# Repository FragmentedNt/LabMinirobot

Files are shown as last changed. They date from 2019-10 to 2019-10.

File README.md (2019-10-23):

# What's this

* sn研でやってる子供向けLEGOロボットのソースとか回路とか機械とか

# 数増やしたいんだけど

1. CircuitCase/Case1_2_9V2.stlおよびCircuitCase/Cover3.ncdを印刷/切削
1. Circuit_v1/ にあるGコードで基板削ってはんだ付け
1. Arduino nanoを用意してminirobo_rmlab/minirobo_rmlab.inoを書き込み
1. SBDBT(3.3V/5V問わず)を用意する
1. MPLAB IPEで sbdbt_ps3_v4/sbxbt_ps3.X/dist/default/production/sbxbt_ps3.X.production.hexを書き込む
1. Done!

# 改善要望

* 回路ケースここまで大きくなくていい
  * LEGOポッチつけたのは大失敗なので消して適当なLEGO板貼り付けるのがベスト
* DCジャック，配線通してはんだ付けするのクソでは？
  * ほんまそれな
* TA8428Kがディスコン
  * 8SOICのイカした後継ICが出てるはず

# 連絡先

* fragmentednt@zoho.com

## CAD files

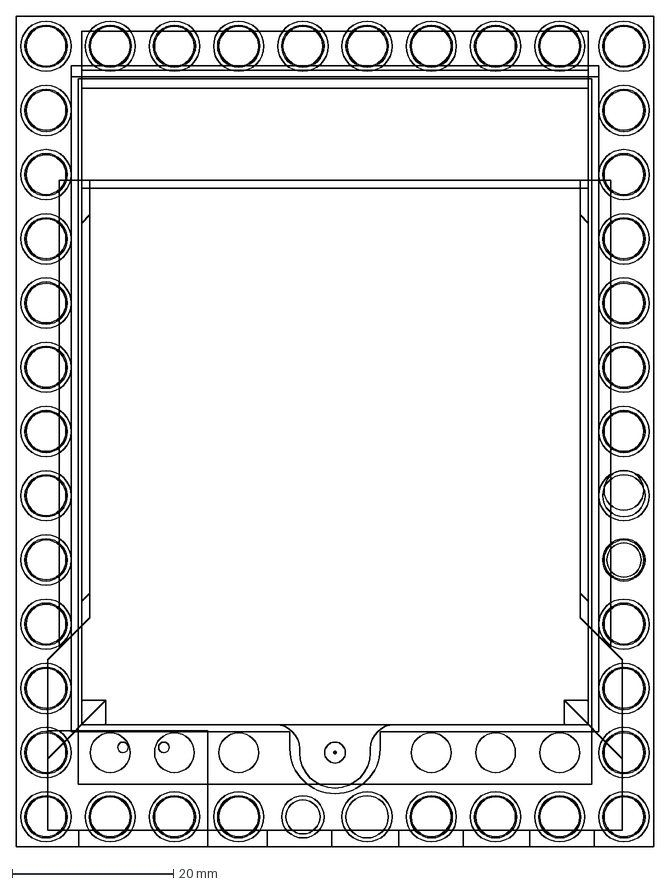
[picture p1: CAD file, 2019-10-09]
CircuitCase/Cover3.dxf
79.1 x 103.1 mm

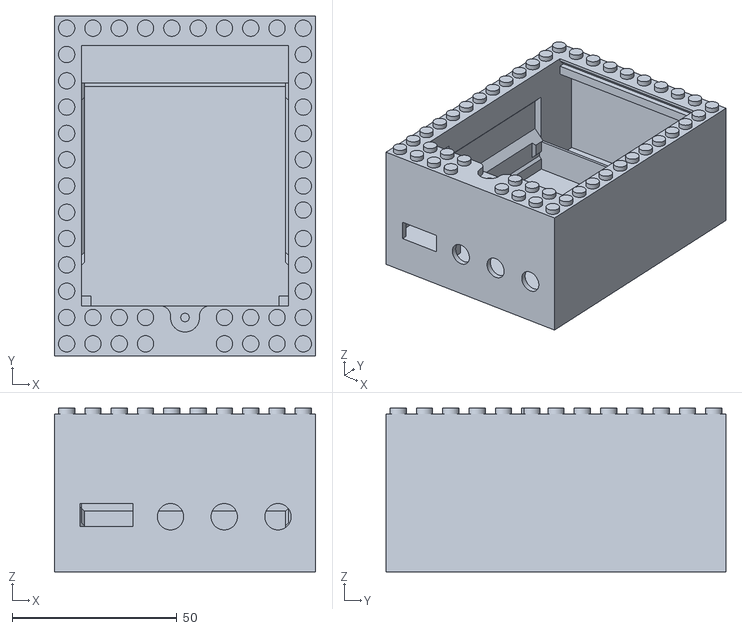
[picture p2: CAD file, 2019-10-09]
CircuitCase/Case1_2_9V2.stl
79.2 x 103.1 x 49.7

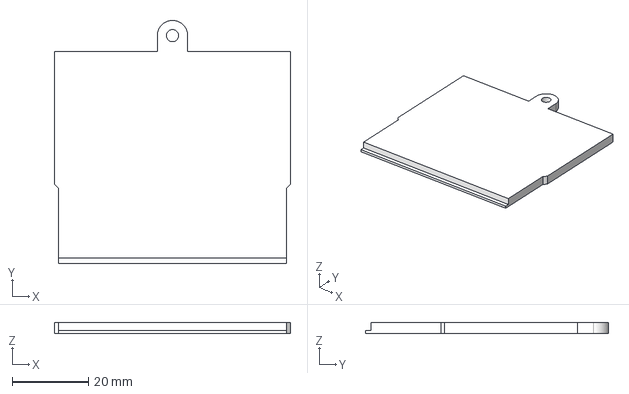
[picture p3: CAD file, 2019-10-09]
CircuitCase/Cover.igs
61.9 x 63.8 x 3.00 mm

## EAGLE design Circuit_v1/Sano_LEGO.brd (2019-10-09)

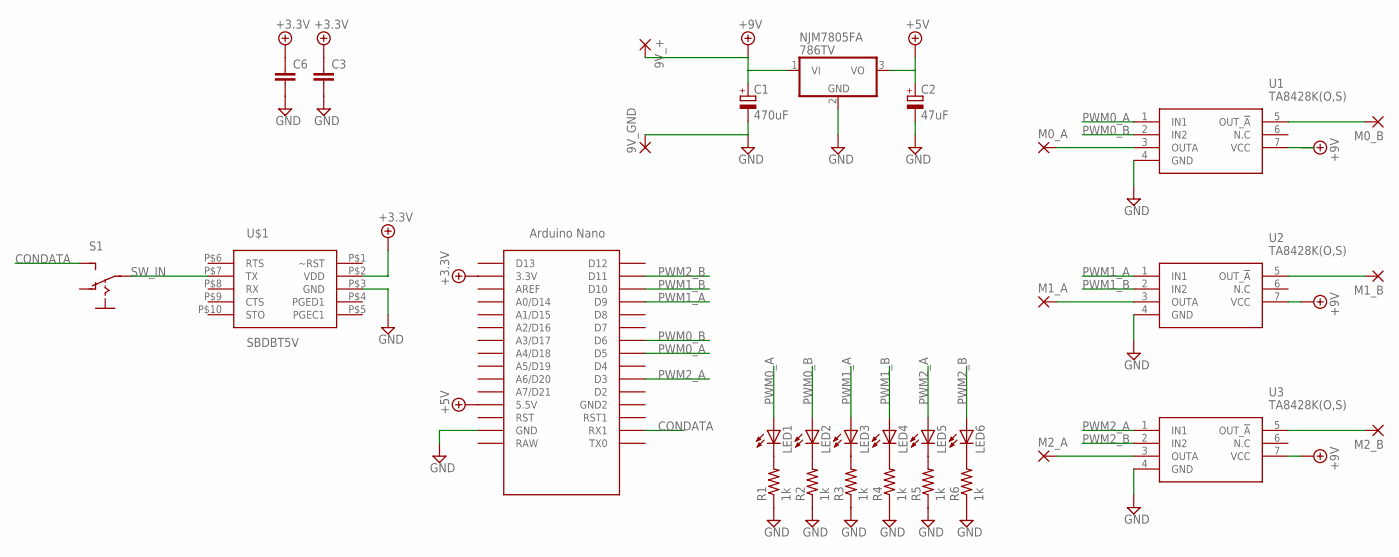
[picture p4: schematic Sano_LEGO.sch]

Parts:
9V_+, 9V_GND: 3,81/1,4
C1: 470uF; E3,5-10
C2: 47uF; E2-5
C3, C6: C-EU025-025X050; C025-025X050
LED1, LED2, LED3, LED4, LED5, LED6: LED3MM
M0_A, M0_B, M1_A, M1_B, M2_A, M2_B: 3,81/1,4
NJM7805FA: 786TV; TO220V
R1, R2, R3, R4, R5, R6: 1k; R1608
S1: S-SWITCHSMALL; DS
U1, U2, U3: TA8428K(O,S); HSIP7-P-2.54_1
U$1: SBDBT5V; SBDBT
U$2: NANO

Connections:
+3.3V: C3.1, C6.1, U$1.P$2 (VDD), U$2.3.3V
+5V: C2.+, NJM7805FA.3 (VO), U$2.5V (5.5V)
+9V: 9V_+.1, C1.+, NJM7805FA.1 (VI), U1.7 (VCC), U2.7 (VCC), U3.7 (VCC)
CONDATA: S1.P$3 (S), U$2.RX1
GND: 9V_GND.1, C1.-, C2.-, C3.2, C6.2, NJM7805FA.2 (GND), R1.1, R2.1, R3.1, R4.1, R5.1, R6.1, U1.4 (GND), U2.4 (GND), U3.4 (GND), U$1.P$3 (GND), U$2.GND
unnamed: LED1.K (C), R1.2
unnamed: M0_A.1, U1.3 (OUTA)
unnamed: M0_B.1, U1.5 (OUT_!A)
unnamed: M1_B.1, U2.5 (OUT_!A)
unnamed: M1_A.1, U2.3 (OUTA)
unnamed: M2_B.1, U3.5 (OUT_!A)
unnamed: M2_A.1, U3.3 (OUTA)
unnamed: LED2.K (C), R2.2
unnamed: LED3.K (C), R3.2
unnamed: LED4.K (C), R4.2
unnamed: LED5.K (C), R5.2
unnamed: LED6.K (C), R6.2
PWM0_A: LED1.A, U1.1 (IN1), U$2.D5
PWM0_B: LED2.A, U1.2 (IN2), U$2.D6
PWM1_A: LED3.A, U2.1 (IN1), U$2.D9
PWM1_B: LED4.A, U2.2 (IN2), U$2.D10
PWM2_A: LED5.A, U3.1 (IN1), U$2.D3
PWM2_B: LED6.A, U3.2 (IN2), U$2.D11
SW_IN: S1.P$2, U$1.P$7 (TX)

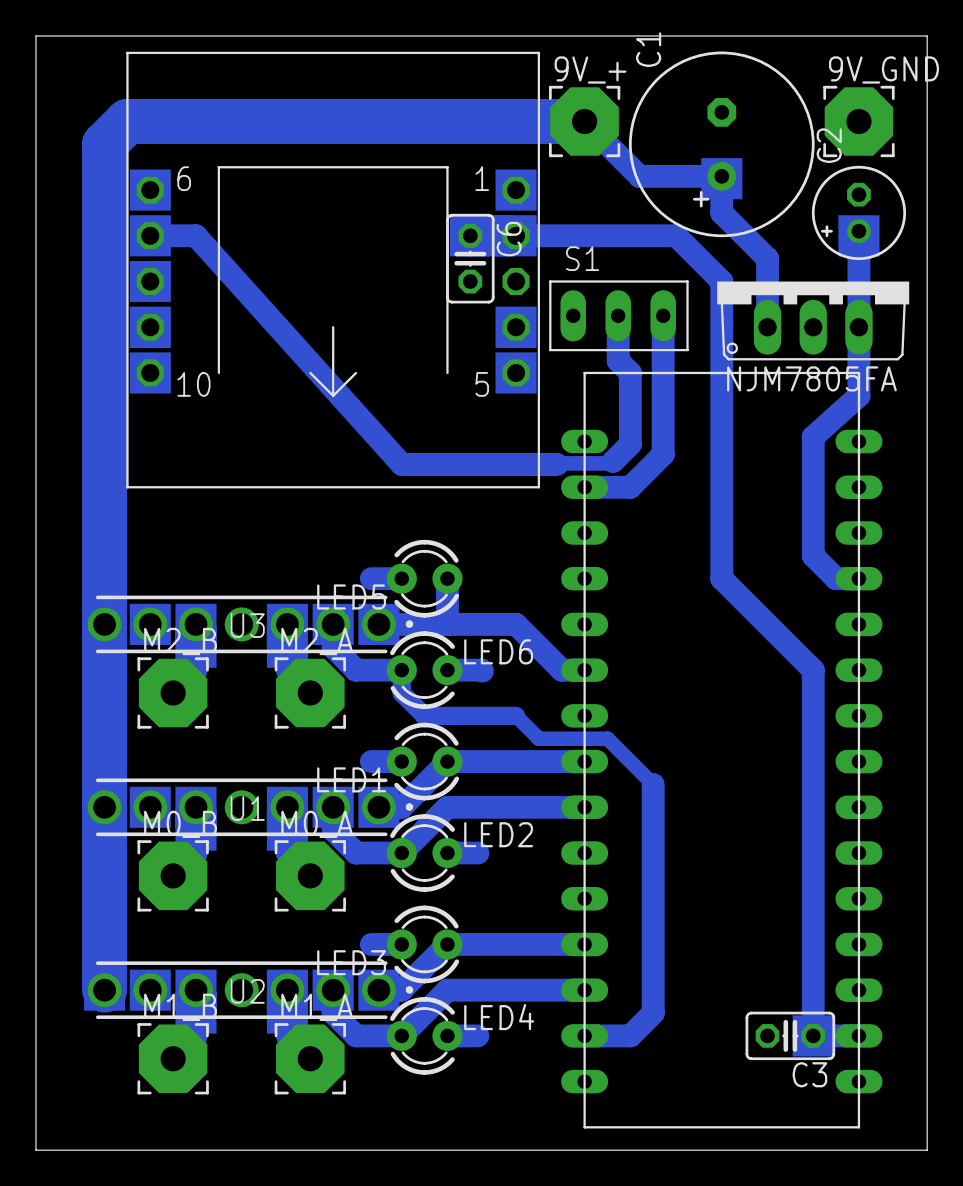
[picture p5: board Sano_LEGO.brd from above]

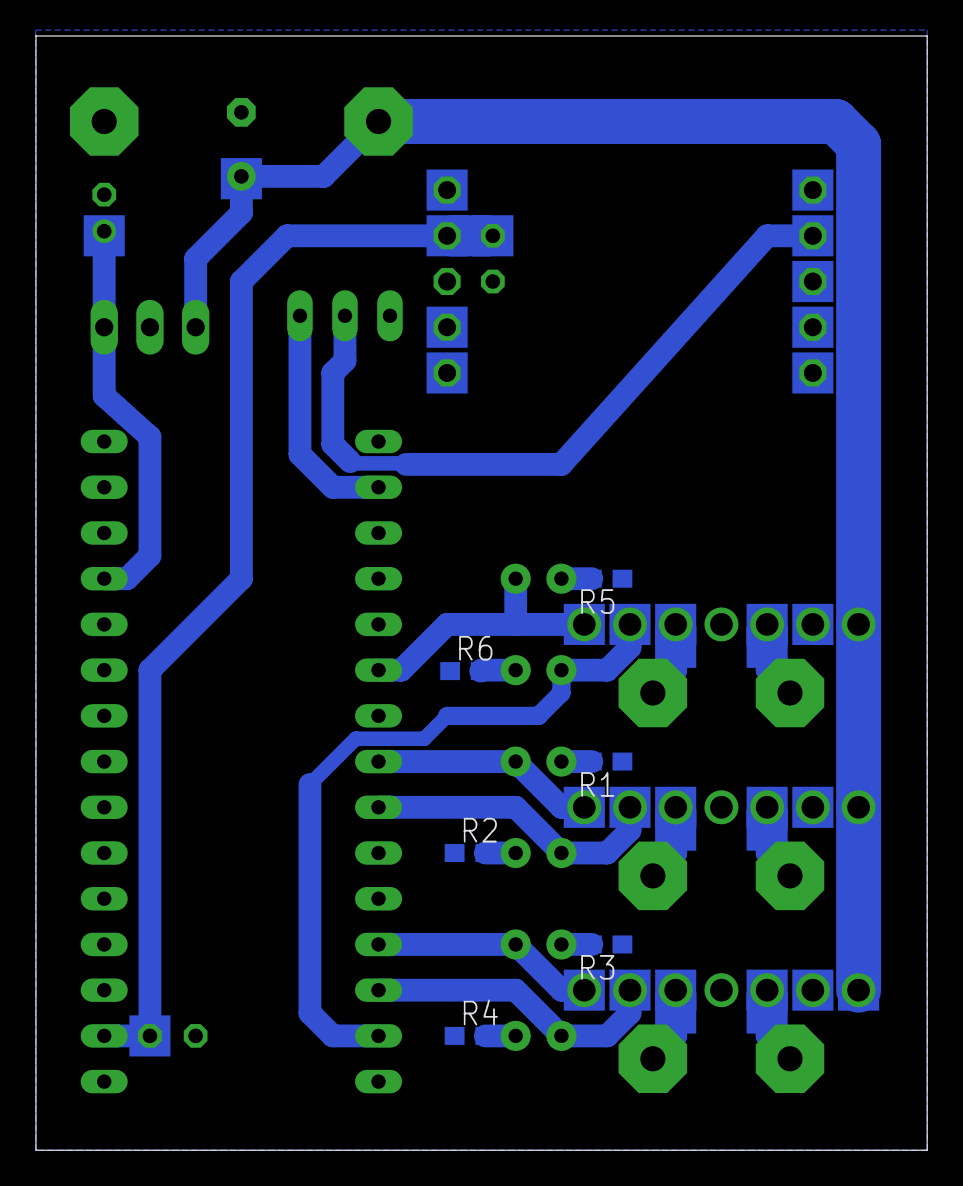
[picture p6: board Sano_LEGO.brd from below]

Board: 2 copper layers, 49.5 x 61.9 mm, 31 parts (6 on the bottom side), 24 nets.

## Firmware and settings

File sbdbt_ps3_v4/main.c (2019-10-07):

// SBDBT/SBXBT Series PS3 / USB Controller Communication Program
//
// Copyright (C) 2012 Kunihiro Shibuya 
// Standalone Pairing modified (C) 2012 Toshihiro Nakatani
// added support controller (C) 2012 Toshihiro Nakatani
// added support controller (C) 2012 Michio Ono

#include <stdlib.h>
#define USE_AND_OR /* To enable AND_OR mask setting */
//#include <ports.h>
//#include <pps.h>
//#include <outcompare.h>
#include "global.h"
#include "btstack/btdebug.h"
#include "btstack/btstack.h"
#include "btstack/hci_cmds.h"
#include "btstack/run_loop.h"
#include "btstack/sdp_util.h"
#include "btstack/hal_tick.h"

#include "btstack/hci.h"
#include "btstack/l2cap.h"
#include "btstack/btstack_memory.h"
#include "btstack/remote_device_db.h"
#include "btstack/rfcomm.h"
#include "btstack/sdp.h"
#include "btstack/hal_tick.h"

#include "TimeDelay.h"

#define	CREDITS					 10

#define	led1_on_mac()			{led1_on(); led1_on_count=clock(); led1_on_state=1;}
#if	USE_SPP_SERVER
static uint8_t		rfcomm_send_credit=CREDITS;
static uint8_t		rfcomm_channel_nr = 1;
static uint16_t		rfcomm_channel_id;
static uint8_t		__attribute__ ((aligned(2))) spp_service_buffer[128];
#endif

static volatile clock_t			timer_counter=0;
static unsigned					led1_on_count=0;
static uint8_t					led1_on_state=0;
char							lineBuffer[50];
static uint8_t					startup_state=0;
void (*usb_tick_handler)(void);	//sibu

#if	SEND_ON_DIFFERENT_DATA || NEUTRAL_DATA_SUPPRESS
static char					lastsendbuf[FORMAT_DATALEN];
#endif
#if	UART1_MINIMUM_INTERVAL
static clock_t					lastsendtime=0;
#endif

#define	BUTTON_STATE_INIT	0
WORD	sixaxis_control_channel_id=0;
static WORD	sixaxis_interrupt_channel_id=0;

hci_transport_t * hci_transport_picusb_instance();

#if defined(__PIC24FJ64GB004__)
	_CONFIG1(WDTPS_PS2048 & FWPSA_PR128 & WINDIS_OFF & FWDTENDEF & ICSDEF & GWRP_OFF & GCP_OFF & JTAGEN_OFF)
	_CONFIG2(POSCMOD_NONE & I2C1SEL_PRI & IOL1WAY_OFF & OSCIOFNC_ON & FCKSM_CSDCMD & FNOSC_FRCPLL & PLL96MHZ_ON & PLLDIV_DIV2 & IESO_OFF)
	_CONFIG3(WPFP_WPFP0 & SOSCSEL_IO & WUTSEL_LEG & WPDIS_WPDIS & WPCFG_WPCFGDIS & WPEND_WPENDMEM)
	_CONFIG4(DSWDTPS_DSWDTPS3 & DSWDTOSC_LPRC & RTCOSC_SOSC & DSBOREN_OFF & DSWDTEN_OFF)
#else

    #error Cannot define configuration bits.

#endif

BYTE        deviceAddress;  // Address of the device on the USB
bd_addr_t addr_global;

BOOL InitializeSystem ( void )
{
   #if defined(__PIC24FJ64GB004__)
	    {
	        unsigned int pll_startup_counter = 600;
	        CLKDIVbits.PLLEN = 1;
	        while(pll_startup_counter--);
	    }

		AD1PCFG = 0xffff;
	    CLKDIV = 0;    // Set PLL prescaler (1:1)
    #endif

	on_setup();
	led1_setup();
	led2_setup();
	led1_on();
	led2_on();
	u1rx_setup();
	u1tx_setup();
	u1cts_setup();
	u1rts_setup();
	sto_setup();
	assoc_setup();
	pairen_setup();

    // Init UART
    UART1Init(BAUDRATE1);
#if	STO_SERIAL
    UART2Init();
#endif

    return TRUE;
} // InitializeSystem

BOOL USB_ApplicationEventHandler ( BYTE address, USB_EVENT event, void *data, DWORD size )
{
    #ifdef USB_BLUETOOTH_SUPPORT_SERIAL_NUMBERS
        BYTE i;
    #endif

    // Handle specific events.
    switch ((int)event)
    {
        case EVENT_BLUETOOTH_ATTACH:
            if (size == sizeof(BLUETOOTH_DEVICE_ID))
            {
                deviceAddress   = ((BLUETOOTH_DEVICE_ID *)data)->deviceAddress;
                log_info( "Bluetooth device attached - event, deviceAddress=%d\r\n",deviceAddress );
                #ifdef USB_BLUETOOTH_SUPPORT_SERIAL_NUMBERS
                    for (i=1; i<((BLUETOOTH_DEVICE_ID *)data)->serialNumberLength; i++)
                    {
                        log_info("%c", ((BLUETOOTH_DEVICE_ID *)data)->serialNumber[i] );
                    }
	                log_info( "\r\n" );
                #endif
                return TRUE;
            }
            break;

        case EVENT_BLUETOOTH_DETACH:
            deviceAddress   = 0;
            log_info( "Bluetooth device detached - event\r\n" );
            return TRUE;

        case EVENT_BLUETOOTH_TX_CMD_DONE:           // The main state machine will poll the driver.
            return TRUE;

        case EVENT_BLUETOOTH_TX_ACL_DONE:           // The main state machine will poll the driver.
            return TRUE;

        case EVENT_BLUETOOTH_RX_EVENT_DONE:
			if(*(DWORD*)data){
				event_bluetooth_rxEvent_done((WORD)(*(DWORD*)data));
			}
            return TRUE;

        case EVENT_BLUETOOTH_RX_ACL_DONE:
			if(*(DWORD*)data){
				event_bluetooth_rxAcl_done((WORD)(*(DWORD*)data));
			}
            return TRUE;

        case EVENT_VBUS_REQUEST_POWER:
            // We'll let anything attach.
            return TRUE;

        case EVENT_VBUS_RELEASE_POWER:
            // We aren't keeping track of power.
            return TRUE;

        case EVENT_HUB_ATTACH:
            log_info( "\r\n***** USB Error - hubs are not supported *****\r\n" );
            return TRUE;
            break;

        case EVENT_UNSUPPORTED_DEVICE:
            log_info( "\r\n***** USB Error - device is not supported *****\r\n" );
            return TRUE;
            break;

        case EVENT_CANNOT_ENUMERATE:
            log_info( "\r\n***** USB Error - cannot enumerate device *****\r\n" );
            return TRUE;
            break;

        case EVENT_CLIENT_INIT_ERROR:
            log_info( "\r\n***** USB Error - client driver initialization error *****\r\n" );
            return TRUE;
            break;

        case EVENT_OUT_OF_MEMORY:
            log_info( "\r\n***** USB Error - out of heap memory *****\r\n" );
            return TRUE;
            break;

        case EVENT_UNSPECIFIED_ERROR:   // This should never be generated.
            log_info( "\r\n***** USB Error - unspecified *****\r\n" );
            return TRUE;
            break;

        case EVENT_SUSPEND:
        case EVENT_DETACH:
        case EVENT_RESUME:
        case EVENT_BUS_ERROR:
            return TRUE;
            break;

        default:
            break;
    }

    return FALSE;

} // USB_ApplicationEventHandler


#define	ANALOG_STATE_INIT		0x80

unsigned int sixaxis_button_state=BUTTON_STATE_INIT;
BYTE sixaxis_home;
BYTE sixaxis_lx=ANALOG_STATE_INIT;
BYTE sixaxis_ly=ANALOG_STATE_INIT;
BYTE sixaxis_rx=ANALOG_STATE_INIT;
BYTE sixaxis_ry=ANALOG_STATE_INIT;

uint8_t getsum(void *buf,size_t size)
{
	const uint8_t	*p=(uint8_t*)buf;
	uint8_t			ret=0;

	for(;size;size--){
		ret+=*p++;
	}
	return ret;
}

uint8_t conv_analog(uint8_t ai)
{
	uint8_t ret;

#if	STICK_NUTRAL_VALUE==64
	ai>>=1;
#endif
	if(ai>(STICK_NUTRAL_VALUE+STICK_DEADZONE)) {
	#if	USE_STICK_FOR_DIGITAL
		//スティックをデジタル的に扱う
		ret=STICK_MAXIMUM_VALUE;
	#else
		//スティックをアナログ的に扱う
		#if STICK_RESOLUTION
			ret=((ai+(STICK_RESOLUTION-1))/STICK_RESOLUTION)*STICK_RESOLUTION-1;
		#else
			ret=ai;
		#endif
		#if	STICK_MAXIMUM_VALUE<255
		if(ret>STICK_MAXIMUM_VALUE){
			ret=STICK_MAXIMUM_VALUE;
		}
		#endif
	#endif
	} else if(ai<(STICK_NUTRAL_VALUE-STICK_DEADZONE)) {
	#if	USE_STICK_FOR_DIGITAL
		//スティックをデジタル的に扱う
		ret=STICK_MINIMUM_VALUE;
	#else
		//スティックをアナログ的に扱う
		#if STICK_RESOLUTION
			ret=((ai/STICK_RESOLUTION)*STICK_RESOLUTION;
		#else
			ret=ai;
		#endif
		#if	STICK_MINIMUM_VALUE
			if(ret<STICK_MINIMUM_VALUE){
				ret=STICK_MINIMUM_VALUE;
			}
		#endif
	#endif
	} else {
		ret=STICK_NUTRAL_VALUE;	//ニュートラルとして扱う
	}

	return ret;
}

//ニュートラル時のデータ
#if FORMAT_RCB3
	const uint8_t neutral_packet[]={0x80,0x00,0x00,0x40,0x40,0x40,0x40,};
#elif	FORMAT_RCB4
	const uint8_t neutral_packet[]={0x0D,0x00,0x02,0x50,0x03,0x00,0x00,0x00,0x40,0x40,0x40,0x40,};	
#elif	FORMAT_RPU
	const uint8_t neutral_packet[]={0x4B,0xFF,0xFF,0xFF,0x80,0x80,0x80,0x80,0xF3};	
	const uint8_t disconnect_packet[]={0x4B,0xFF,0xFF,0xFF,0x80,0x80,0x80,0x80,0xFF};	
	const uint8_t connect_packet[]={0x4B,0xFF,0xFF,0xFF,0x80,0x80,0x80,0x80,0xFB};	
#endif

clock_t clock(void)
{
	return timer_counter;
}

void UART1PutBuf(char *buf,size_t size)
{
#if	UART1_MINIMUM_INTERVAL
	for(;(clock()-lastsendtime)<UART1_MINIMUM_INTERVAL;){
	}
	lastsendtime=clock();
#endif

	for(;size;size--){
		UART1PutChar(*buf++);
	}
	return;
}

void out_button_state(void)
{
	int	pos=0;
	//電文　固定値
#if FORMAT_RCB3
	lineBuffer[pos++]=0x80; //1バイト目:0x80固定
#elif	FORMAT_RCB4
	//lineBuffer[pos++]=0xBB;
	//lineBuffer[pos++]=0xEE;
	//lineBuffer[pos++]=0x02;
	//lineBuffer[pos++]=0x50;
	//lineBuffer[pos++]=0x03;
	//lineBuffer[pos++]=0x00;
#elif	FORMAT_RPU
	lineBuffer[pos++]=0x4B;
	lineBuffer[pos++]=0xFF;
#else
#error	"Unknown format"
#endif
	//電文の作成
#if FORMAT_RCB3
	lineBuffer[pos++]=(sixaxis_button_state>>8)&0xff;	//2バイト目:ボタン状態デジタル1
	lineBuffer[pos++]=(sixaxis_button_state>>0)&0xff;	//3バイト目:ボタン状態デジタル2
	//xyxy
	lineBuffer[pos++]=conv_analog(sixaxis_lx);		//4バイト目:左スティックX状態(0x00-0x7f) アナログのようでデジタル
	lineBuffer[pos++]=conv_analog(sixaxis_ly);		//5バイト目:左スティックY状態(0x00-0x7f) アナログのようでデジタル
	lineBuffer[pos++]=conv_analog(sixaxis_rx);		//6バイト目:右スティックX状態(0x00-0x7f) アナログのようでデジタル
	lineBuffer[pos++]=conv_analog(sixaxis_ry);		//7バイト目:右スティックY状態(0x00-0x7f) アナログのようでデジタル
	lineBuffer[pos]=(getsum(lineBuffer,pos)&0x7f);		//8バイト目:チェックサム下位7ビット
	pos++;
#elif	FORMAT_RCB4
	lineBuffer[pos++]=(sixaxis_button_state>>0)&0xff;	//1バイト目:ボタン状態デジタル2
        lineBuffer[pos++]=(sixaxis_button_state>>8)&0xff;	//2バイト目:ボタン状態デジタル1
        lineBuffer[pos++]=(sixaxis_home)&0xff;                  //3バイト目:ボタン状態デジタル1
        lineBuffer[pos++]=conv_analog(0xFF-sixaxis_ly);		//4バイト目:左スティックy状態(0x00-0x7f) アナログのようでデジタル
	lineBuffer[pos++]=conv_analog(sixaxis_lx);		//5バイト目:左スティックx状態(0x00-0x7f) アナログのようでデジタル
	lineBuffer[pos++]=conv_analog(0xFF-sixaxis_ry);		//6バイト目:右スティックy状態(0x00-0x7f) アナログのようでデジタル
	lineBuffer[pos++]=conv_analog(sixaxis_rx);		//7バイト目:右スティックx状態(0x00-0x7f) アナログのようでデジタル
	lineBuffer[pos++] = (lineBuffer[0] + lineBuffer[1] + lineBuffer[2] + lineBuffer[3] + lineBuffer[4] + lineBuffer[5] + lineBuffer[6] + 0x7c + 0x7c) & 0xFF;		//8バイト目:チェックサム
        lineBuffer[pos++] = 0x7C;                                 //9バイト目:チェックサム
        lineBuffer[pos] = 0x7C;                                 //10バイト目:チェックサム
	pos++;
#elif	FORMAT_RPU
	lineBuffer[pos++]=((sixaxis_button_state>>8)&0xff)^0xff;	//2バイト目:ボタン状態デジタル1
	lineBuffer[pos++]=((sixaxis_button_state>>0)&0xff)^0xff;	//3バイト目:ボタン状態デジタル2
	lineBuffer[pos++]=conv_analog(sixaxis_rx);			//5バイト目:右スティックX状態(0x00-0x7f) アナログのようでデジタル
	lineBuffer[pos++]=conv_analog(sixaxis_ry);			//6バイト目:右スティックY状態(0x00-0x7f) アナログのようでデジタル
	lineBuffer[pos++]=conv_analog(sixaxis_lx);			//7バイト目:左スティックX状態(0x00-0x7f) アナログのようでデジタル
	lineBuffer[pos++]=conv_analog(sixaxis_ly);			//8バイト目:左スティックY状態(0x00-0x7f) アナログのようでデジタル
	lineBuffer[pos++]=0xF3;								//9バイト目:0xF3固定
#endif

#if	SEND_ON_DIFFERENT_DATA
	//前回と差があった時のみ送信
	if(memcmp(lastsendbuf,lineBuffer,pos)){			//前回送信データと差がある場合のみ送信
		led1_on_mac();									//赤色LED点灯
		UART1PutBuf(lineBuffer,pos);						//データ送信

#if	NEUTRAL_ADDITIONAL_PACKETS
		if(!memcmp(neutral_packet,lineBuffer,sizeof(neutral_packet))){	//このデータはニュートラルか
			unsigned nc;
			for(nc=0;nc<NEUTRAL_ADDITIONAL_PACKETS;nc++){
				UART1PutBuf(lineBuffer,pos);				//ニュートラルのデータの場合は追加で送る
			}
		}
#endif
		memcpy(lastsendbuf,lineBuffer,pos);				//送信したデータを比較用に保存
	}
#else
	//連続送信
#if	UART1_MINIMUM_INTERVAL
	if((clock()-lastsendtime)>=UART1_MINIMUM_INTERVAL){
#endif
#if	NEUTRAL_DATA_SUPPRESS
		if(memcmp(neutral_packet,lineBuffer,sizeof(neutral_packet)) || memcmp(lastsendbuf,lineBuffer,pos)){	//このデータはニュートラルか
#endif
			if(UART1GetBufferSpace()>=pos){
				led1_on_mac();									//赤色LED点灯
				UART1PutBuf(lineBuffer,pos);						//データ送信

#if	NEUTRAL_ADDITIONAL_PACKETS
				if(!memcmp(neutral_packet,lineBuffer,sizeof(neutral_packet))){	//このデータはニュートラルか
					unsigned nc;
					for(nc=0;nc<NEUTRAL_ADDITIONAL_PACKETS;nc++){
						UART1PutBuf(lineBuffer,pos);				//ニュートラルのデータの場合は追加で送る
					}
				}
#endif
#if	NEUTRAL_DATA_SUPPRESS
				memcpy(lastsendbuf,lineBuffer,pos);				//送信したデータを比較用に保存
#endif
			}
#if	NEUTRAL_DATA_SUPPRESS
		}
#endif
#if	UART1_MINIMUM_INTERVAL
	}
#endif
#endif

	return;
}

void init_button_state(void)
{
	sixaxis_button_state=BUTTON_STATE_INIT;
	sixaxis_lx=ANALOG_STATE_INIT;
	sixaxis_ly=ANALOG_STATE_INIT;
	sixaxis_rx=ANALOG_STATE_INIT;
	sixaxis_ry=ANALOG_STATE_INIT;

#if	FORMAT_RPU
	memcpy(lineBuffer,disconnect_packet,sizeof(disconnect_packet));
#if	SEND_ON_DIFFERENT_DATA || NEUTRAL_DATA_SUPPRESS
	memcpy(lastsendbuf,disconnect_packet,sizeof(disconnect_packet));
#endif
	UART1PutBuf(lineBuffer,sizeof(disconnect_packet));
#else
	out_button_state();
#endif
}

static int enable_sixaxis(uint16_t channel)
{
    uint8_t cmd_buf[6];
    cmd_buf[0] = 0x53;// HID BT Set_report (0x50) | Report Type (Feature 0x03)
    cmd_buf[1] = 0xF4;// Report ID
    cmd_buf[2] = 0x42;// Special PS3 Controller enable commands
    cmd_buf[3] = 0x03;
    cmd_buf[4] = 0x00;
    cmd_buf[5] = 0x00;

	return l2cap_send_internal(channel,cmd_buf,6);
}

static int set_sixaxis_led(uint16_t channel,int led)
{
	memcpy(lineBuffer+2,OUTPUT_REPORT_BUFFER,OUTPUT_REPORT_BUFFER_SIZE);
    lineBuffer[0] = 0x52;// HID BT Set_report (0x50) | Report Type (Output 0x02)
    lineBuffer[1] = 0x01;// Report ID
	//lineBuffer[11] |= (uint8_t)(((uint16_t)led & 0x0f) << 1);    

	return l2cap_send_internal(channel,(uint8_t*)lineBuffer,HID_BUFFERSIZE);
}

#if	USE_DUALSHOCK3_RUMBLE
static int set_sixaxis_rumble(uint16_t channel,int rumble)
{
	memcpy(lineBuffer+2,OUTPUT_REPORT_BUFFER,OUTPUT_REPORT_BUFFER_SIZE);
    lineBuffer[0] = 0x52;// HID BT Set_report (0x50) | Report Type (Output 0x02)
    lineBuffer[1] = 0x01;// Report ID
	lineBuffer[3] = (rumble==1)?10:0;		//rightDuration
	lineBuffer[4] = (rumble==1)?0xff:0;		//rightPower
	lineBuffer[5] = (rumble==2)?10:0;		//leftDuraion
	lineBuffer[6] = (rumble==2)?0xff:0;		//leftPower

	return l2cap_send_internal(channel,(uint8_t*)lineBuffer,HID_BUFFERSIZE);
}
#endif

static uint8_t sixaxis_init_state=0;

static void l2cap_control_packet_handler(uint8_t packet_type, uint16_t channel, uint8_t *packet, uint16_t size)
{
	if (packet_type == HCI_EVENT_PACKET){
		switch(packet[0]){
		case L2CAP_EVENT_INCOMING_CONNECTION:
			log_info("L2CAP_EVENT_INCOMING_CONNECTION\n");
			l2cap_accept_connection_internal(channel);
			break;
		case L2CAP_EVENT_CHANNEL_OPENED:
	        if (packet[2]) {
	            log_info("control Connection failed\n\r");
	            return;
		    }
			log_info("control Connected\n\r");
			sixaxis_control_channel_id=channel;
			break;
		case L2CAP_EVENT_CHANNEL_CLOSED:
			log_info("L2CAP_CHANNEL_CLOSED\n");
			sixaxis_control_channel_id=0;
			sixaxis_init_state=0;
			init_button_state();
			break;
		case L2CAP_EVENT_CREDITS:
			switch(sixaxis_init_state){
			case	1:
				sixaxis_init_state++;
				DelayMs(1000);
				set_sixaxis_led(channel,1);
#if	FORMAT_RPU
				memcpy(lineBuffer,connect_packet,sizeof(connect_packet));
#if	SEND_ON_DIFFERENT_DATA || NEUTRAL_DATA_SUPPRESS
				memcpy(lastsendbuf,connect_packet,sizeof(connect_packet));
#endif
				UART1PutBuf(lineBuffer,sizeof(connect_packet));
#endif
				break;
			default:
				break;
			}
			break;
		default:
			log_info("l2cap:unknown(%02x)\n",packet[0]);
			break;
		}	
	}
}

static void l2cap_interrupt_packet_handler(uint8_t packet_type, uint16_t channel, uint8_t *packet, uint16_t size)
{
	if (packet_type == HCI_EVENT_PACKET){
		switch(packet[0]){
		case L2CAP_EVENT_INCOMING_CONNECTION:
			log_info("L2CAP_EVENT_INCOMING_CONNECTION\n");
			l2cap_accept_connection_internal(channel);
			break;
		case L2CAP_EVENT_CHANNEL_OPENED:
	        if (packet[2]) {
	            log_info("interrupt Connection failed\n\r");
	            return;
		    }
			log_info("interrupt Connected\n\r");
			sixaxis_interrupt_channel_id=channel;
			break;
		case L2CAP_EVENT_CHANNEL_CLOSED:
			log_info("L2CAP_CHANNEL_CLOSED\n");
			sixaxis_interrupt_channel_id=0;
			sixaxis_init_state=0;
			init_button_state();
			break;
		case L2CAP_EVENT_CREDITS:
			switch(sixaxis_init_state){
			case	0:
				sixaxis_init_state++;
				enable_sixaxis(sixaxis_control_channel_id);
				break;
			default:
				break;
			}			break;
		default:
			log_info("l2cap:unknown(%02x)\n",packet[0]);
			break;
		}	
	}
	if (packet_type == L2CAP_DATA_PACKET && size && packet[0]==0xa1){
		sixaxis_process_packet(packet+1,size-1);
	}
}
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
int main ( void )
{
	RestartWatchdog();

#ifdef __DEBUG
	xdev_out(UART2PutChar);
#endif

    // Initialize the processor and peripherals.
    if ( InitializeSystem() != TRUE )
    {
        log_info( "\r\n\r\nCould not initialize " LOCAL_NAME " - system.  Halting.\r\n\r\n" );
#ifdef	__DEBUG
        while (1);
#else
		Reset();
#endif
	}
    if ( USBHostInit(0) == TRUE )
    {
        log_info( "\r\n\r\n***** " LOCAL_NAME " Initialized *****\r\n\r\n" );
    }
    else
    {
        log_info( "\r\n\r\nCould not initialize " LOCAL_NAME " - USB.  Halting.\r\n\r\n" );
#ifdef	__DEBUG
        while (1);
#else
		Reset();
#endif
    }

   // Main Processing Loop
    while(1)
    {
		if(deviceAddress){
#if	USE_USB_HID_CONTROLLER
			if(gc_DevData.ID.vid == 0x05B8 && gc_DevData.ID.pid == 0x1004){//add @naka_at_kure
				startup_state=1;
				dev_elecom_u3312s();
			}else if(gc_DevData.ID.vid == 0x05B8 && gc_DevData.ID.pid == 0x1006){//add @naka_at_kure
				startup_state=1;
				dev_elecom_u3412s();
			}else if(gc_DevData.ID.vid == 0x0079 && gc_DevData.ID.pid == 0x0006){//add @micutil
				startup_state=1;
				dev_dragonrise();
			}else if(gc_DevData.ID.vid == 0x046D){
				if(gc_DevData.ID.pid == 0xC219){//add @micutil
					startup_state=1;
					dev_logicool_f710();
				}else if(gc_DevData.ID.pid == 0xC218){//add @micutil
					startup_state=1;
					dev_logicool_f510();
				}else if(gc_DevData.ID.pid == 0xC21F){// logicool f710 X mode
				}else if(gc_DevData.ID.pid == 0xC21E){// logicool f510 X mode
				}else if(gc_DevData.ID.pid == 0xC22F){// logicool f710 and f510 initialize
				}else{
					log_info( "\r\n usb controller not found\r\n\r\n" );
					break;
				}
			}else
#endif
			//connect PS3Controller
			if(gc_DevData.ID.vid == 0x054Cul && gc_DevData.ID.pid == 0x0268ul){
				startup_state=1;
				dev_sony_ps3();
			}else{
				log_info( "\r\n usb controller not found\r\n\r\n" );
				break;
			}
		}
        // This demo does not check for overcurrent conditions.  See the
        // USB Host - Data Logger for an example of overcurrent detection
        // with the PIC24F and the USB PICtail Plus.

        // Maintain USB Host State
        USBHostTasks();
		//Idle();
        //if (CheckForNewAttach()){
		//	break;
        //}
    }

	init_button_state();
	DelayMs(1000);

	//led2_off();

	/// GET STARTED with BTstack ///
	btstack_memory_init();
    run_loop_init(RUN_LOOP_EMBEDDED);
	
    // init HCI
	hci_transport_t    * transport = hci_transport_picusb_instance();
	bt_control_t       * control   = NULL;
    hci_uart_config_t  * config    = NULL;
    remote_device_db_t * remote_db = (remote_device_db_t *) &remote_device_db_memory;
	hci_init(transport, config, control, remote_db);

    // use eHCILL
//    bt_control_cc256x_enable_ehcill(1);
    
    // init L2CAP
    l2cap_init();
    l2cap_register_packet_handler(packet_handler);

	l2cap_register_service_internal(NULL, l2cap_control_packet_handler, PSM_HID_CONTROL, 160);
	l2cap_register_service_internal(NULL, l2cap_interrupt_packet_handler, PSM_HID_INTERRUPT, 160);

#if	USE_SPP_SERVER
	// init RFCOMM
    rfcomm_init();
    rfcomm_register_packet_handler(packet_handler);
    rfcomm_register_service_with_initial_credits_internal(NULL, rfcomm_channel_nr, 100, CREDITS);  // reserved channel, mtu=100, 1 credit

    // init SDP, create record for SPP and register with SDP
    sdp_init();

	memset(spp_service_buffer, 0, sizeof(spp_service_buffer));
    service_record_item_t * service_record_item = (service_record_item_t *) spp_service_buffer;
    sdp_create_spp_service( (uint8_t*) &service_record_item->service_record, 1, "SPP");
    log_info("SDP service buffer size: %u\n\r", (uint16_t) (sizeof(service_record_item_t) + de_get_len((uint8_t*) &service_record_item->service_record)));
    sdp_register_service_internal(NULL, service_record_item);
#endif

	// turn on!
	hci_power_control(HCI_POWER_ON);

#if	!USE_WRITE_STORED_LINK_KEY
extern linked_list_t db_mem_link_keys;
void load_link_keys(remote_device_db_t * lpremote_device_db);
void print_link_keys(linked_list_t list);
	load_link_keys(remote_db);
	print_link_keys(db_mem_link_keys);
#endif

    led1_off();

//DelayMs(1000);

    // go!
    run_loop_execute();	

    return 0;

} // main


void hal_tick_init(void)
{
	usb_tick_handler=NULL;
}

void hal_tick_set_handler(void (*tick_handler)(void))
{
	usb_tick_handler=tick_handler;
}

void hal_tick_event(void)
{
	timer_counter++;

	RestartWatchdog();

#ifndef	__DEBUG
	if(!startup_state && timer_counter>5000){
		Reset();
	}
#endif

    if (sixaxis_control_channel_id){
        if(timer_counter&0x100){
            led2_off();
			assoc_l();
        }else{
            led2_on();
			assoc_h();
        }
		sto_h();
    }else{
        led2_on();
		sto_l();
		assoc_l();
    }

	if(led1_on_state && (timer_counter-led1_on_count)>LED1_ON_COUNT){
		led1_off();
		led1_on_state=0;
	}

	// call tick handler
	if(usb_tick_handler){
		usb_tick_handler();
	}
}

#if	USE_SPP_SERVER
void sendchar(void)
{
	int	ch;
	unsigned len;

	if(is_rfcomm_send_avail(rfcomm_channel_id)){
		//can't send rfcomm now
		return;
	}

	for(len=0;len<sizeof(lineBuffer);len++){
		ch=UART1GetChar();
		if(ch<0){
			break;
		}
		//log_info("UART1GetChar=%c\r\n",ch);
		lineBuffer[len]=ch;
	}
	if(len){
	    led1_on_mac();
        int err = rfcomm_send_internal(rfcomm_channel_id, (uint8_t*) lineBuffer, len);
        if (err) {
            log_error("rfcomm_send_internal -> error %d", err);
        }
	}
}
#elif USE_DUALSHOCK3_RUMBLE
void sendchar(void)
{
	int ch;

	for(;;){
		ch=UART1GetChar();
		if(ch<0){
			break;
		}
		if(sixaxis_control_channel_id){
			set_sixaxis_rumble(sixaxis_control_channel_id,ch-'0');
		}
	}
}
#endif
/*************************************************************************
 * EOF main.c
 */

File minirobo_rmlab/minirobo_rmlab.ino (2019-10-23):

#include "TM0.h"
#include "MotorDriverTA8428K.h"
#include "pscon.h"
#include <math.h>

void setup() {
  // put your setup code here, to run once:
	Serial.begin(115200);
	Pscon.init(Serial);
	pinMode(13, OUTPUT);

	// タイマ設定 PWM周波数変えるのに使用 https://arduinoinfo.mywikis.net/wiki/Arduino-PWM-Frequency
	TCCR0B = (TCCR0B & 0b11111000) | 0x02;
	TCCR1B = (TCCR1B & 0b11111000) | 0x02;
	TCCR2B = (TCCR2B & 0b11111000) | 0x02;

	// TCCRレジスタ弄っちゃうとTimer0の動作周波数が変わってmicros()とかmillis()とかが狂うのでそれをなんとなく補正する自作クラス
	TM0.init();

	// MDのピン配置
	MD0.init(5,  6, true);
	MD1.init(9, 10, true, true);
	MD2.init(3, 11, true);
}


void loop() {
  // put your main code here, to run repeatedly:
	float forward = 0, turn = 0; 
	static bool indivisualTwoWheel = false;

	if(!Pscon.getData())
	{
		//Pscon.debug();

		if(Pscon.Fall_L3())
			indivisualTwoWheel = !indivisualTwoWheel;
		if(Pscon.Fall_Select())
			MD0.inversion();
		if(Pscon.Fall_Start())
			MD1.inversion();
			
		if(indivisualTwoWheel)
		{
			MD0.set(2 * Pscon.Left_Y());
			MD1.set(2 * Pscon.Right_Y());
		}
		else
		{
			if(abs(Pscon.D_Left_Y()) > 0.3)
				forward = Pscon.D_Left_Y();
			if(abs(Pscon.D_Right_X()) > 0.3)
				turn = Pscon.D_Right_X();
			MD0.set(255 * forward + 255 * turn);
			MD1.set(255 * forward - 255 * turn);
		}
		
		if (Pscon.R1())
			MD2.set(100);
		else if (Pscon.R2())
			MD2.set(-100);
		else
			MD2.set(0);
	}
	else
	{
		MD0.set(0);
		MD1.set(0);
		MD2.set(0);
	}
	
	
	//printTimeSpan();
	//demo();
	
	if(indivisualTwoWheel)
		blinkLED(100);
	else
		blinkLED(500);
	
	TM0.Delay(20); 

}

void printTimeSpan()
{
	static unsigned long prev_time = 0, current_time = 0;
	current_time = TM0.Micros();
	Serial.println(current_time - prev_time);
	prev_time = TM0.Micros();
}

void blinkLED(unsigned long ts)
{
	static unsigned long ms = 0;
	unsigned long mi = TM0.Millis();
	if (mi - ms > ts)
	{
		ms = mi;
		PINB |= _BV(5);	// Arduino nanoのPB5(D13番)に接続されているLEDを操作
						// AVRの仕様でPINxに書き込むと出力が反転する(通常の出力レジスタはPORTx)
	}
}

void demo()
{
	static int ms = 0;
	int mi = TM0.Millis();
	if (mi - ms < 2000)
	{
		MD0.set(0);
		MD1.set(0);
		MD2.set(0);
	}
	else if (mi - ms < 4000)
	{
		MD0.set(100);
		MD1.set(100);
		MD2.set(100);
	}
	else if (mi - ms < 6000)
	{
		MD0.set(0);
		MD1.set(0);
		MD2.set(0);
	}
	else if (mi - ms < 8000)
	{
		MD0.set(-100);
		MD1.set(-100);
		MD2.set(-100);
	}
	else
	{
		ms = mi;
	}
}

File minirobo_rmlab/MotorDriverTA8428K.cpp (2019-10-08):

// 
// 
// 

#include "MotorDriverTA8428K.h"


void MotorDriverTA8428KClass::init(byte pinA, byte pinB, bool brake = false, bool inverse = false, bool pwm_enable = true)
{
	this->pinA = pinA;
	this->pinB = pinB;
	pinMode(pinA, OUTPUT);
	pinMode(pinB, OUTPUT);
	this->brake = brake;
	this->inverse = inverse;
	this->pwm = pwm_enable;
	prev_power = 0;
	if (pwm)
	{
		analogWrite(pinA, 0);
		analogWrite(pinB, 0);
	}
	else
	{
		digitalWrite(pinA, LOW);
		digitalWrite(pinB, LOW);
	}
	TM0.DelayMicroseconds(100);
	set(0);
}

void MotorDriverTA8428KClass::set(short power)
{
	if (inverse)
		power *= -1;
	
	if (prev_power != power)
	{
		prev_power = power;
		if (pwm)
		{
			analogWrite(pinA, 0);
			analogWrite(pinB, 0);
		}
		else
		{
			digitalWrite(pinA, LOW);
			digitalWrite(pinB, LOW);
		}
		TM0.DelayMicroseconds(100);
	}

	if (power > 0)
	{
		if (power > 255)	power = 255;
		if (pwm)
		{
			analogWrite(pinA, power);
			analogWrite(pinB, 0);
		}
		else
		{
			digitalWrite(pinA, HIGH);
			digitalWrite(pinB, LOW);
		}
	}
	else if (power < 0)
	{
		if (power < -255)	power = -255;
		if (pwm)
		{
			analogWrite(pinA, 0);
			analogWrite(pinB, -power);
		}
		else
		{
			digitalWrite(pinA, LOW);
			digitalWrite(pinB, HIGH);
		}
	}
	else
	{
		if (brake)
		{
			if (pwm)
			{
				analogWrite(pinA, 255);
				analogWrite(pinB, 255);
			}
			else
			{
				digitalWrite(pinA, HIGH);
				digitalWrite(pinB, HIGH);
			}
		}
		else 
		{
			if (pwm)
			{
				analogWrite(pinA, 0);
				analogWrite(pinB, 0);
			}
			else
			{
				digitalWrite(pinA, LOW);
				digitalWrite(pinB, LOW);
			}
		}
	}
}

/// <summary>
/// 
/// </summary>
/// <param name="power"></param>
/// <param name="brake"></param>
void MotorDriverTA8428KClass::set(short power, byte brake)
{
	this->brake = brake;
	set(power);
}

void MotorDriverTA8428KClass::inversion()
{
	inverse = !inverse;
}


MotorDriverTA8428KClass MD0, MD1, MD2;

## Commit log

2018-08-25 Copy from Arduino solution
2018-08-29 psconクラス作成
2018-08-29 PSコンの読み取り実装 動確は未だ duty，degree計算は未実装
2018-08-30 pscon周り修正
2018-08-30 モタドラ駆動クラスを追加
2018-09-02 キャッシュを削除し.gitignoreの変更を反映
2018-09-02 Timer0を用いる標準関数をラップするクラスの作成 PWMの周波数を変更すると影響が出るため
2018-09-02 wiring.hを書き換えるほうが正しそうなのでTM0.h，TM0.cppを除外
2018-09-02 Revert "wiring.hを書き換えるほうが正しそうなのでTM0.h，TM0.cppを除外"
    This reverts commit 7ff5ff75d863093fb7d0a68c891945ebe1ebf533.
    [minirobo_rmlab.ino]
2018-09-02 PWM周波数変更
2018-09-02 delayMicrosecondはTimer0と無関係なことが判明したので変更 なお精度
2018-09-02 いろいろ
2018-09-03 PWM周波数変更 分周無しではモタドラICの挙動に変化が見られなかったため
2018-10-14 ディジタルピンモードを追加
2018-11-17 visual studioがなんかした感じ
2019-10-07 add: SBDBTのプロジェクトを追加
2019-10-07 update: 左スティック前進，右スティック旋回に変更
2019-10-08 update: 独立駆動2輪とモードチェンジができるように変更
2019-10-08 制御周期を20msにして正しくFallを取れるようにした
2019-10-09 update: MPLABがなんかやったっぽい
2019-10-09 add: 回路データ追加
    [Sano_LEGO.brd, Sano_LEGO.sch]
2019-10-09 add: 回路ケースCADを追加（バイナリ含む）
    [Case1_2_9V2.stl, Cover.igs, Cover3.dxf]
2019-10-23 update: コメント追加してVisualStudio拡張用のファイル削除
